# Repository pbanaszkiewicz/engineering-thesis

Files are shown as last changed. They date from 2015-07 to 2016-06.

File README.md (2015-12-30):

# Emergency Stop for an Autonomous Vehicle
## A Bachelor's Engineering Thesis project

This repository contains my BEng Thesis and project files.
The Thesis itself will be in Polish, but other resources should be
in English.

## Compilation

You can create a `main.pdf` containing the Thesis with following command:

```bash
$ make pdf
```

To remove all the debris from LaTeX use `make clean`.

## Credits

LaTeX class for AGH-UST specific representation of the Thesis was made by
M. Szpyrka and others (see `aghdpl.cls` for more).

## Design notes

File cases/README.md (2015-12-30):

Module cases
============

Cases presented here are based on the Arduino Leonardo and Uno containers done by
Zygmunt Wojcik (@zygmuntw).

Original work: https://github.com/zygmuntw/3D-Printed-Case-for-Arduino

# License

Zygmunt's work (and therefore this work) is licensed under
[Creative Commons Attribution-ShareAlike 3.0 Unported](http://creativecommons.org/licenses/by-sa/3.0/)
license.

# Modifications

Modifications I introduced:

* removed wholes for USB and other plugs
* moved PCB legs so that they work with Arduino Pro
* PCB legs: instead of pins I made wells (ie. substract instead of union)
* resized the case for module B and moved PCB legs around a little.

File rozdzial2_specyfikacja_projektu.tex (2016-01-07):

\chapter{Wykonanie projektu}
\label{cha:specyfikacja_projektu}

W tym rozdziale opisane zostało wykonanie projektu zgodnie z wymaganiami postawionymi w rozdziale \ref{cha:wstep}.

%---------------------------------------------------------------------------

\section{Opis części sprzętowej}
\label{sec:opis_cz_sprzetowej}

W poniższym rozdziale została opisana platforma sprzętowa modułów A i B oraz ich współdziałanie z innymi komponentami, m.in. z zasilaniem akumulatorowym czy z przekaźnikiem w samochodzie elektrycznym.

\subsection{Moduł A}
\label{subsec:modul_a}

Jest to moduł bazowy, tj. trzymany przez operatora w dłoni. Ze względu na użycie Arduino Pro 328 5V 16MHz \cite{Ard00} (zob. zdjęcie \ref{fig:arduino_pro}) jako platformy sprzętowej, ma on niewielkie wymiary.

\begin{figure}[h]
	\centering
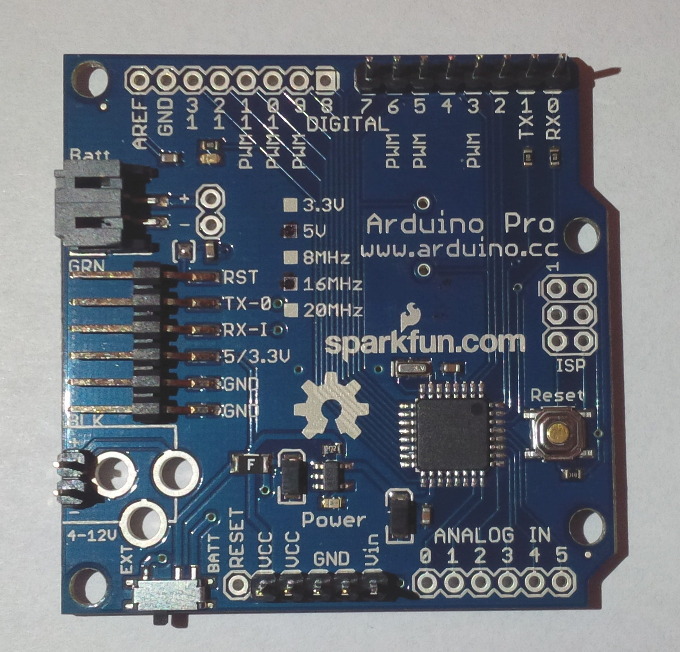
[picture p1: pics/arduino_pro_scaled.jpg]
	
	\caption{\label{fig:arduino_pro}Platforma sprzętowa Arduino Pro 328 5V 16MHz (zdjęcie: Piotr Banaszkiewicz).}
\end{figure}

\raggedbottom

\subsection{Moduł B}
\label{subsec:modul_b}

Jest to moduł, który został zamontowany w samochodzie. Jako platformę użyte zostało ponownie Arduino Pro 328 5V 16MHz \cite{Ard00} (zob. zdjęcie \ref{fig:arduino_pro}). Podstawowa funkcja, tj. odłączanie i załączanie silnika elektrycznego, odbywa się za pomocą przekaźnika ASR-90DD-H firmy Anly Electronics (zob. zdjęcie \ref{fig:SSR_relay} i rozdział \ref{subsec:odlaczanie_zalaczanie_silnika}).

\begin{figure}[h]
	\centering
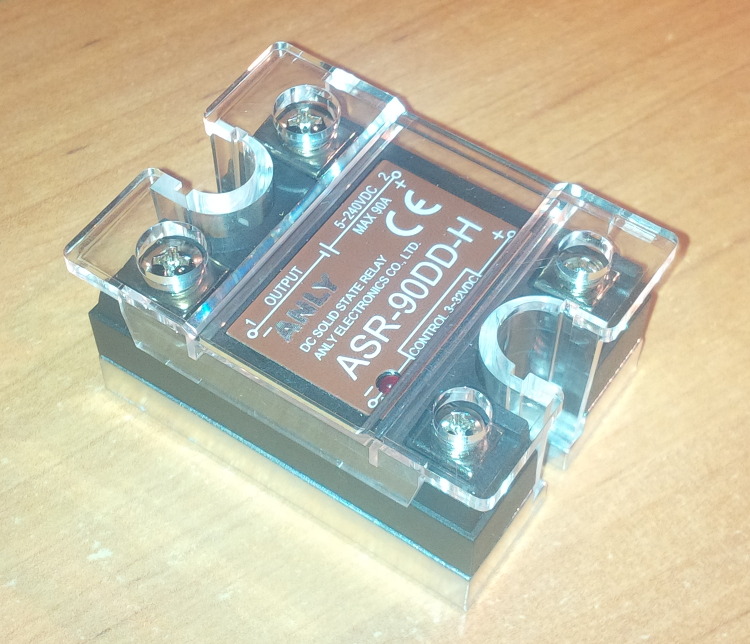
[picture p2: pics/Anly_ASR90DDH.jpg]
	
	\caption{\label{fig:SSR_relay}Przekaźnik półprzewodnikowy ASR-90DD-H  (zdjęcie: Piotr Banaszkiewicz).}
\end{figure}

\subsection{Zasilanie}
\label{subsec:zasilanie}

Obydwa moduły sprzętowe są zasilane z powerbanków Solo5 10000 mAh firmy Romoss. Posiadają one wbudowane różne zabezpieczenia, m.in.: natężeniowe (dla zachowania żywotności), temperaturowe czy zwarciowe (ang. \textit{short-circuit}). Mają również układ, który wyłącza powerbank w sytuacji, gdy prąd ładowania jest bardzo niewielki \cite{Romoss}.

Moduły A i B pobierają bardzo niewiele prądu (zmierzone: między \SI{20}{\milli\ampere} a \SI{50}{\milli\ampere}), więc aby powstrzymać powerbanki przed rozłączaniem zwarto masę i źródło energii dwunastoma (w przypadku modułu A) lub trzynastoma (w przypadku modułu B) rezystorami \SI{910}{\ohm} wpiętymi równolegle.

Połączenie równoległe takiej ilości rezystorów daje dość niską rezystancję zastępczą (teoretycznie: \SI{75.83}{\ohm} dla modułu A, \SI{70}{\ohm} dla modułu B; praktycznie: występują różnice w faktycznych wartościach rezystancji rezystorów, zwłaszcza gdy te się nagrzeją) i pozwala na obniżenie wydzielanego ciepła na rezystorach, co skutkuje:

\begin{itemize}
\item większym poborem prądu, dzięki czemu powerbanki się nie wyłączają,
\item nagrzewaniem rezystorów (z prawa Ohma: $ P = \dfrac{U^2}{R} = \dfrac{(5,1)^2}{900} = 0,0289 [W] $, gdzie \SI{5.1}{\volt} to zmierzone napięcie na rezystorze, a \SI{900}{\ohm} to przybliżona rezystancja nagrzanego rezystora), a więc w przypadku 12 rezystorów położonych bardzo blisko siebie mamy około \SI{0.34}{\watt} wydzielanej mocy w tym miejscu.
\end{itemize}

Ponadto banki energii umożliwiają jednoczesne ładowanie jak i rozładowywanie, tzn. jest możliwe wpięcie źródła zasilania na wejście powerbanku, jak i obciążenia na jego wyjście. Dzięki temu powerbank zasilający moduł B można ładować z portu USB znajdującego się w~samochodzie.

Sama pojemność \SI{10000}{\milli\ampere\hour} teoretycznie\footnote{W praktyce pojemność \SI{10000}{\milli\ampere\hour} jest nieosiągalna, gdyż powerbanki posiadają mechanizmy wydłużające ich żywotność; polega to na ładowaniu akumulatorów powerbanku tylko do pewnego stopnia.} pozwala na zasilanie układu pobierającego \SI{100}{\milli\ampere} przez 100 godzin lub układu pobierającego \SI{200}{\milli\ampere} przez 50 godzin. Każdy z modułów A i B po obciążeniu przez rezystory pobierał między \num{100} a \SI{200}{\milli\ampere}. Poziom naładowania powerbanków można obserwować na ich diodowych wskaźnikach.

\subsection{Komunikacja}
\label{subsec:komunikacja}

Do komunikacji wykorzystano parę modułów radiowych HC-12 433 MHz \cite{HC12}, które łączą się z~platformami sprzętowymi za pomocą łącza szeregowego. Prędkość komunikacji takiego modułu w powietrzu wynosi 5000bps, czyli typowe pakiety przesyłane przez system (zob. rozdział \ref{subsec:format_pakietow}), mające rozmiar $ 4B=32b $ są przesyłane w ułamku sekundy.

\subsection{Obudowy}
\label{subsec:obudowy}

Dla każdego modułu systemu ESAV przygotowano sztywną nakładkę w formie płytki prototypowej (zdjęcia \ref{fig:moduleA_hat} i \ref{fig:moduleB_hat}) z~przylutowanymi komponentami wykorzystywanymi przez dany moduł. Zakładane są one na górne i dolne piny modułów A i B (zob. zdjęcie \ref{fig:arduino_pro}).

\begin{figure}[h]
	\centering
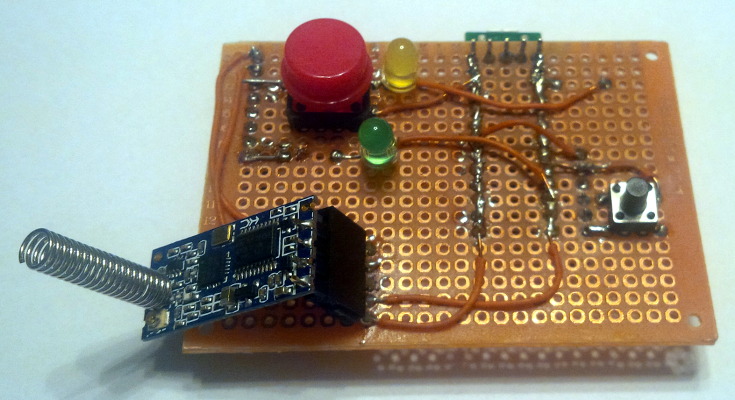
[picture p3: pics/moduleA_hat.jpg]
	
	\caption{\label{fig:moduleA_hat}Nakładka na moduł A (zdjęcie: Piotr Banaszkiewicz).}
\end{figure}

\begin{figure}[h]
	\centering
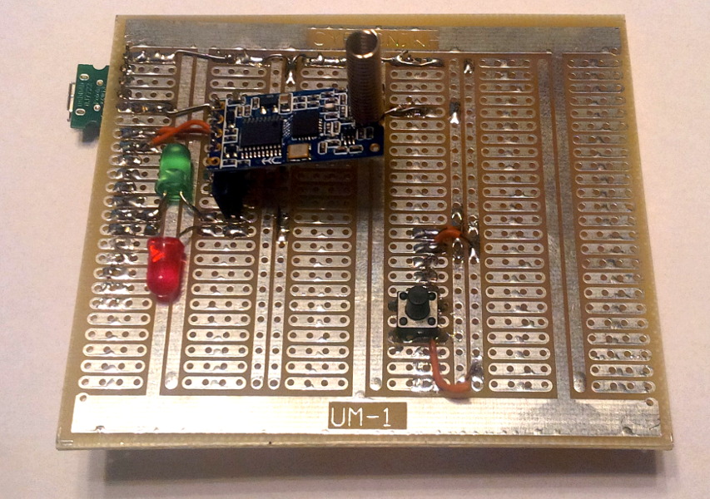
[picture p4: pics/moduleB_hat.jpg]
	
	\caption{\label{fig:moduleB_hat}Nakładka na moduł B (zdjęcie: Piotr Banaszkiewicz).}
\end{figure}

Ponadto na każdą platformę została zaprojektowana obudowa. Na zdjęciu \ref{fig:arduino_pro} widać cztery otwory w platformie Arduino (dwa przy lewej krawędzi płytki PCB oraz dwa przy prawej krawędzi), które zostały użyte do przykręcenia każdej z platform do obudowy.

Obudowy bazują na istniejącym projekcie kontenerów dla Arduino Leonardo oraz Uno wykonanym przez Zygmunta Wojcika  \cite{Woj15}. Ich licencja zezwala na modyfikacje (więcej szczegółów dostępnych jest pod adresem \cite{CasesLicense}).

\begin{figure}[H]
	\centering
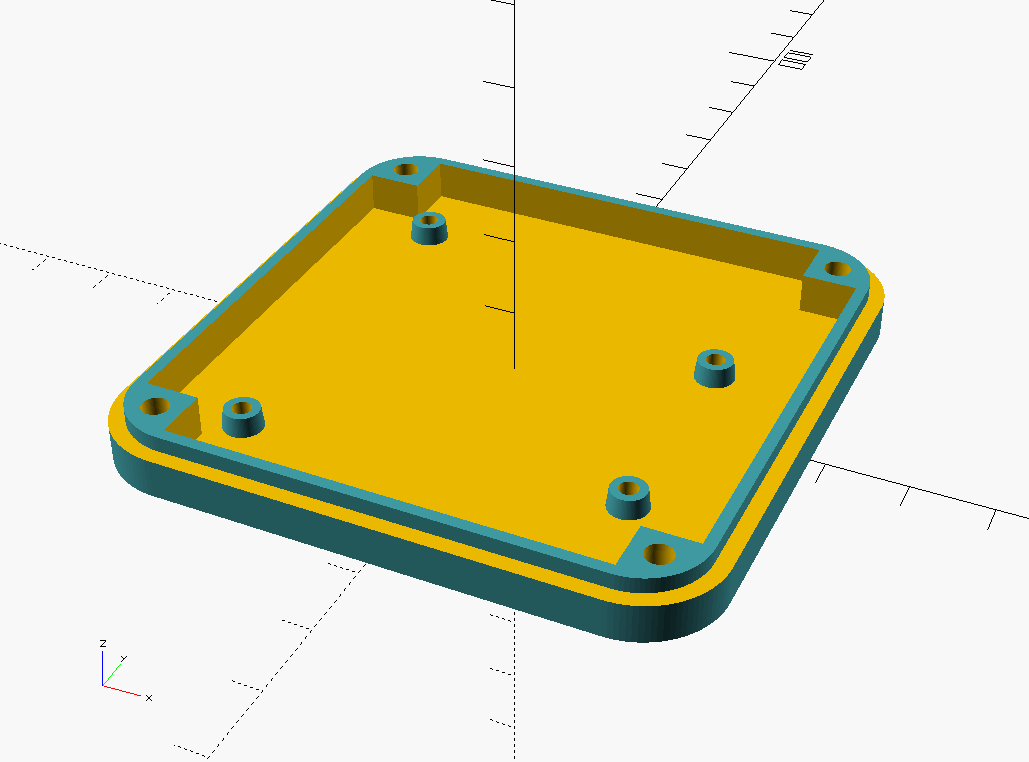
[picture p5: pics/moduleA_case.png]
	
	\caption{\label{fig:moduleA_case}Obudowa modułu A (oryginalny autor: Zygmunt Wojcik, modyfikacje: Piotr Banaszkiewicz \cite{CasesLicense}).}
\end{figure}

\begin{figure}[H]
	\centering
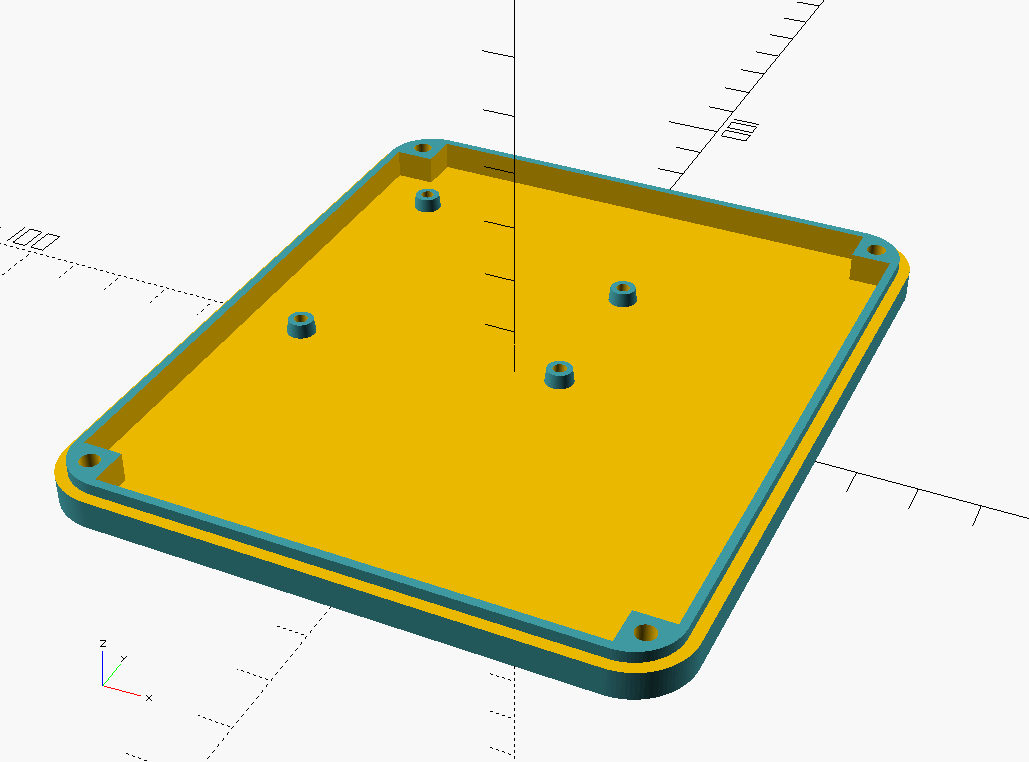
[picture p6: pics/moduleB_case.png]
	
	\caption{\label{fig:moduleB_case}Obudowa modułu B (oryginalny autor: Zygmunt Wojcik, modyfikacje: Piotr Banaszkiewicz \cite{CasesLicense}).}
\end{figure}

\subsection{Schematy połączeń}
\label{subsec:schematy_polaczen}

Symboliczny sposób połączenia modułu A, wejścia zasilającego USB oraz transceivera radiowego został przedstawiony na schemacie \ref{fig:symbolic_schema_A}.

\begin{figure}[H]
	\centering
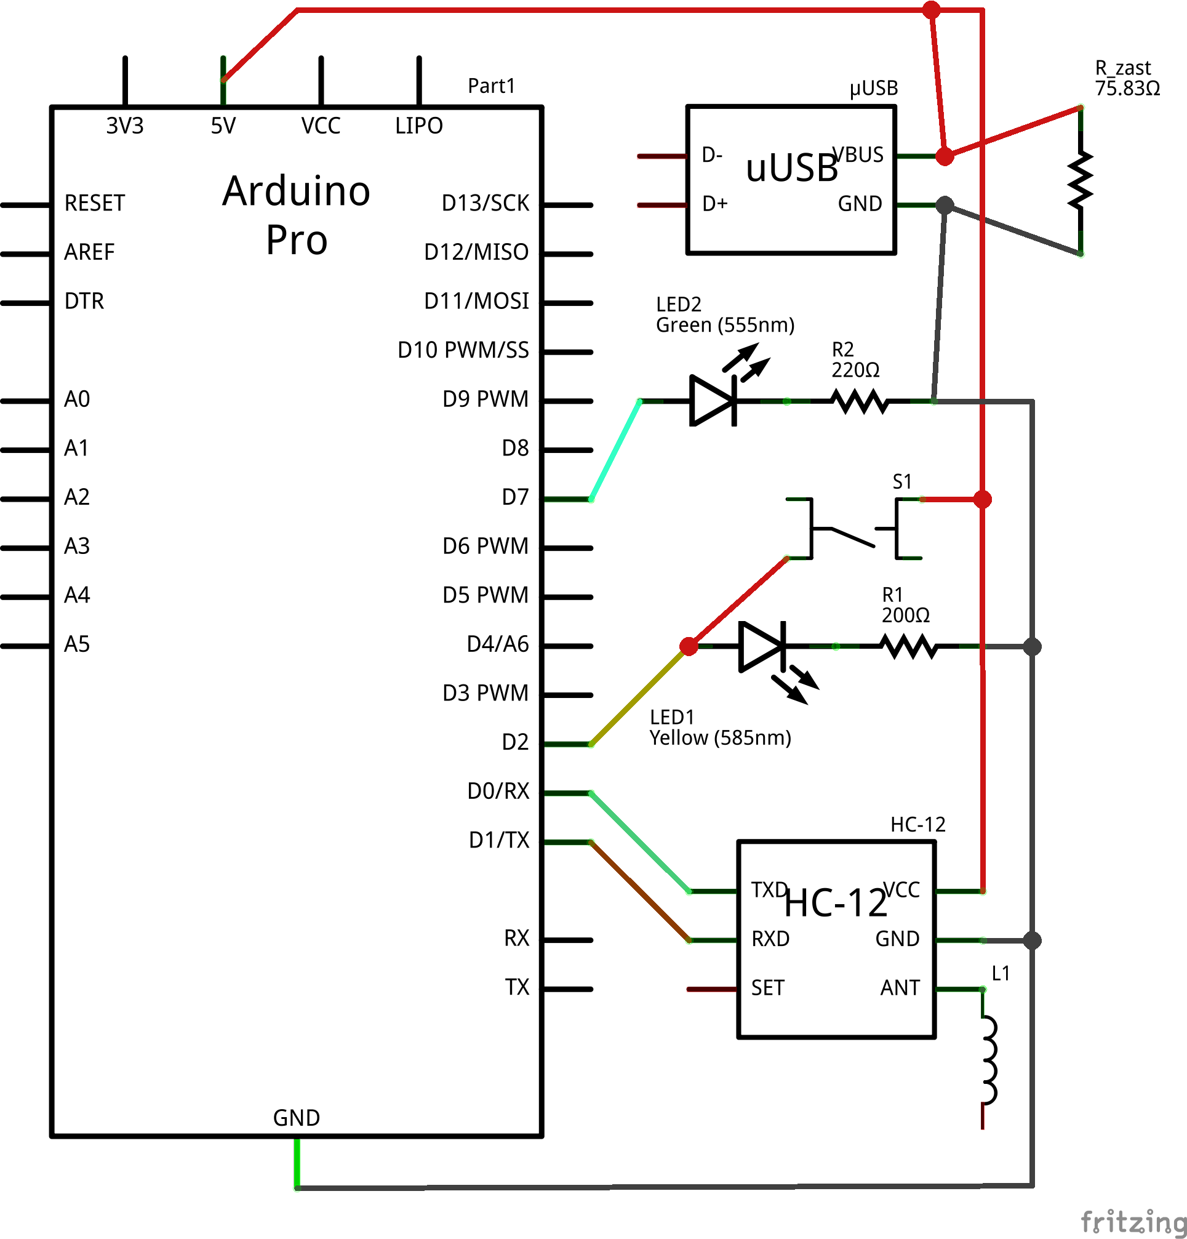
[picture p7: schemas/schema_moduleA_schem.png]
	
	\caption{\label{fig:symbolic_schema_A}Schemat połączeń modułu A wygenerowany w programie Fritzing \cite{Fritzing} (opracowanie własne).}
\end{figure}

Bardzo podobnie wygląda symboliczny schemat połączeń modułu B, z tym że on dodatkowo steruje przekaźnikiem (schemat \ref{fig:symbolic_schema_B}).

\begin{figure}[H]
	\centering
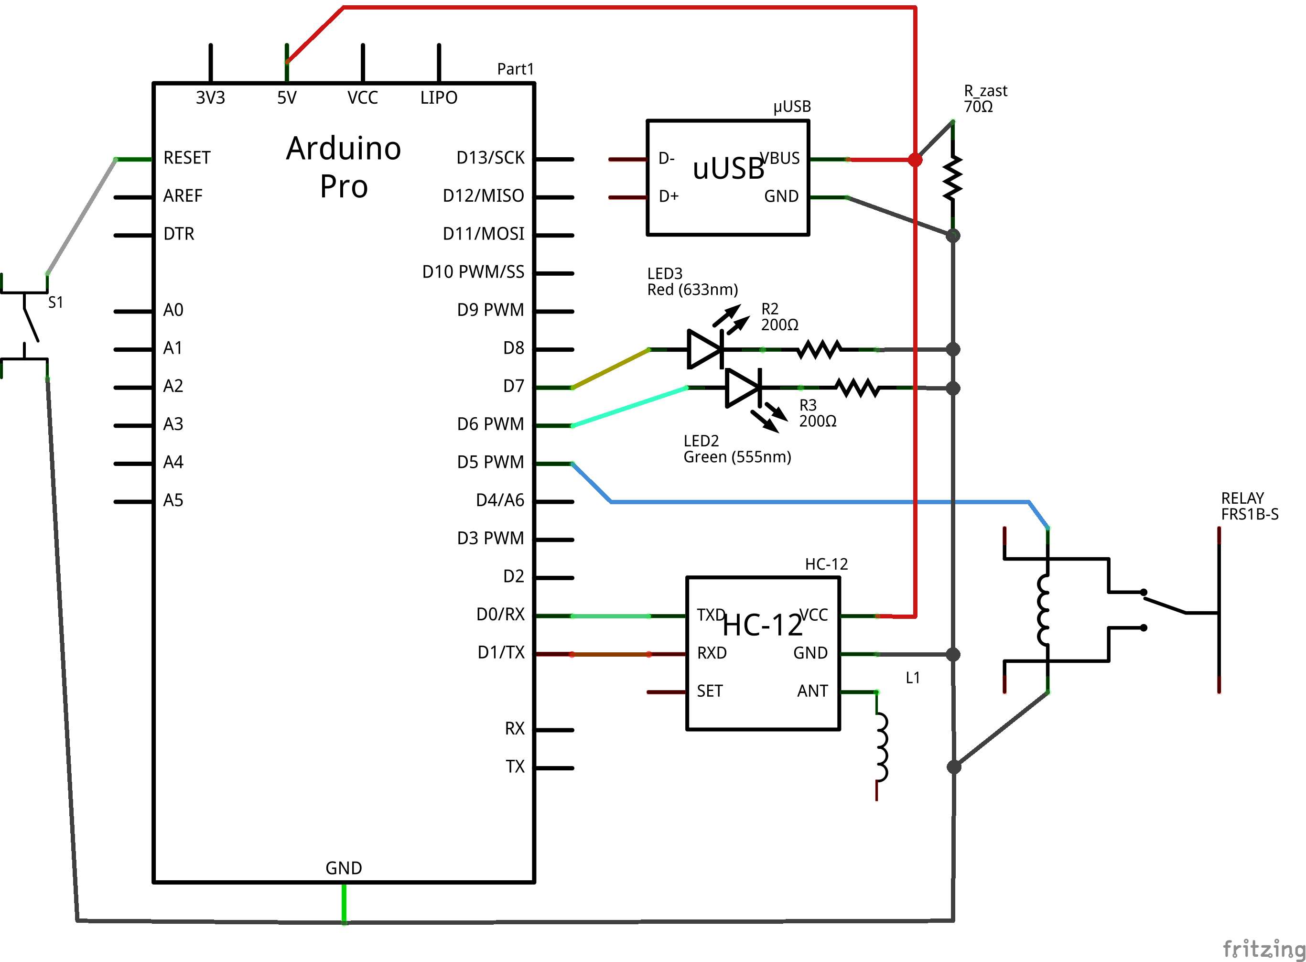
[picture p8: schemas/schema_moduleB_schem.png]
	
	\caption{\label{fig:symbolic_schema_B}Schemat połączeń modułu B wygenerowany w programie Fritzing \cite{Fritzing} (opracowanie własne).}
\end{figure}

\subsection{Odłączanie i załączanie silnika samochodu}
\label{subsec:odlaczanie_zalaczanie_silnika}

Pomiędzy kabel zasilający a moduł sterujący pracą silnika samochodu został wpięty przekaźnik ASR-90DD-H (zob. zdjęcie \ref{fig:SSR_relay}). Moduł sterujący odpowiedzialny jest za przetworzenie napięcia stałego na prąd zmienny poprowadzony bezpośrednio na uzwojenia silnika.

Przekaźnik ASR-90DD-H jest to przekaźnik półprzewodnikowy, a zatem typu \textit{Normally Open}, sterowany napięciem stałym \num{3}--\SI{32}{\volt}. Przekaźnik jest sterowany wyjściem z modułu B (zob. element ,,RELAY'' na schemacie \ref{fig:symbolic_schema_B}).

Według danych producenta, przekaźnik jest w stanie obsłużyć na wyjściu mocy do \SI{90}{\ampere} prądu stałego pod napięciem do \SI{240}{\volt}. Wybrano przekaźnik mocno przekraczający spodziewane natężenie prądu, gdyż zapewnia to mniejsze wydzielanie ciepła (zob. rozdział \ref{subsec:chlodzenie_SSR}).

Niestety producent nie udostępnia schematu elektrycznego przekaźnika w dokumentacji \cite{ASR90DDH}, więc podczas jego montażu zadbano o kilka elementów bezpieczeństwa:

\begin{itemize}
\item zastosowano podkładkę silikonową jako izolator elektryczny,
\item zastosowano radiator chłodzący (widoczny na zdjęciu \ref{fig:radiator}).
\end{itemize}

\begin{figure}[h]
	\centering
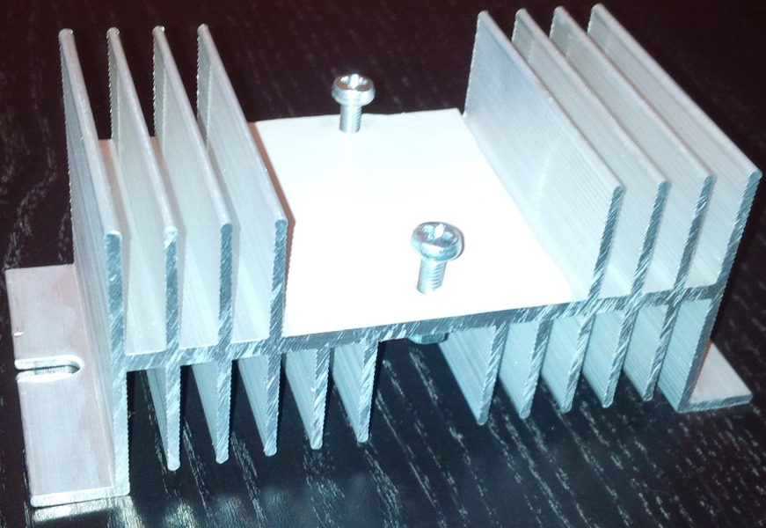
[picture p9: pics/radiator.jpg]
	
	\caption{\label{fig:radiator}Radiator chłodzący przekaźnik SSR (zdjęcie: Piotr Banaszkiewicz).}
\end{figure}

Elementy te zgodne są z zaleceniami polskiego producenta przekaźników, firmy Relpol \cite{RELPOL}.

\subsection{Chłodzenie przekaźnika półprzewodnikowego}
\label{subsec:chlodzenie_SSR}

Przekaźniki półprzewodnikowe z powodu pewnej niskiej oporności własnej w momencie podłączonego wyjścia mocy wydzielają dużą ilość energii w postaci ciepła.

W ramach pracy inżynierskiej przeprowadzono eksperyment polegający na zmierzeniu temperatury obudowy działającego przekaźnika podczas włączonego obciążenia.

Przekaźnik został umieszczony na radiatorze i pracował przez kilka minut (do momentu ustalenia się temperatury) pod stałym obciążeniem. Kamera termowizyjna ostawiona była tak, by mierzyć temperaturę radiatora oraz obudowy przekaźnika. Tabela \ref{tab:eksperyment} zawiera zestawienie długości czasu działania przekaźnika pod obciążeniem, a także uzyskanej na końcu eksperymentu temperatury, natomiast zdjęcia \ref{fig:flir1} i \ref{fig:flir2} ukazują obrazy z kamery termowizyjnej.

\begin{table}[h]
    \centering
    
    \begin{threeparttable}
        \caption{Parametry eksperymentu obciążenia przekaźnika półprzewodnikowego}
        \label{tab:eksperyment}
        
        \begin{tabularx}{0.9\textwidth}{ccccX}
            \toprule
            Czas obciążenia & Napięcie & Natężenie & Temperatura radiatora\tnote{a} & Temperatura obudowy przekaźnika\tnote{a} \\
            \midrule
            \SI{8}{\minute} & \SI{45}{\volt} & \SI{36}{\ampere} & \SI{25}{\celsius} & ok. \SI{60}{\celsius} \\
            \SI{8}{\minute} & \SI{42.5}{\volt} & \SI{43}{\ampere} & \num{25}--\SI{35}{\celsius} & ok. \SI{90}{\celsius} \\
            \bottomrule
        \end{tabularx}
        
        \begin{tablenotes}
            \footnotesize
            \item[a] pod koniec pomiaru
        \end{tablenotes}
        
    \end{threeparttable}
\end{table}

\begin{figure}[H]
	\centering
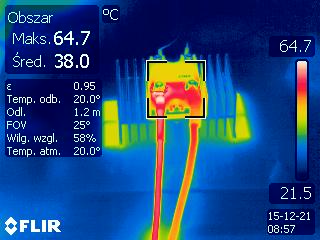
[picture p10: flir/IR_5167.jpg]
	
	\caption{\label{fig:flir1}Obraz uzyskany za pomocą kamery termowizyjnej na koniec trwania eksperymentu z mniejszym obciążeniem (zdjęcie: Marek Długosz).}
\end{figure}

\raggedbottom

\begin{figure}[H]
	\centering
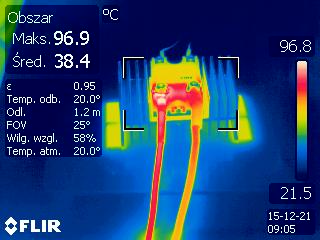
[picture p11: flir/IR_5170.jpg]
	
	\caption{\label{fig:flir2}Obraz uzyskany za pomocą kamery termowizyjnej na koniec trwania eksperymentu z większym obciążeniem (zdjęcie: Marek Długosz).}
\end{figure}

Na powyższych zdjęciach najcieplejszym elementem była śruba służąca do przykręcenia kabla zasilającego. Temperatura ciepłego miejsca na obudowie przekaźnika była o około \SI{15}{\celsius} niższa; uwzględnione to zostało w tabeli \ref{tab:eksperyment} poprzez odjęcie ok. \SI{10}{\celsius} od maksymalnej mierzonej temperatury.

Ponadto należy zauważyć jak niewiele nagrzewał się radiator, do którego przymocowany został przekaźnik. To udowadnia, że jest on wystarczający dla zastosowania w samochodzie.

Na samym końcu należy zauważyć, że przekaźnik nie powinien być w realnych zastosowaniach narażony na tak duże obciążenia przez tak długi czas; według obserwacji, maksymalny prąd chwilowy w trakcie przyspieszania pojazdu i skręcania jednocześnie wynosił około \SI{50}{\ampere}.

%---------------------------------------------------------------------------

\section{Opis części programowej}
\label{sec:opis_cz_programowej}

W tym rozdziale opisano m.in. logikę, algorytmy i struktury danych wykorzystywane przez programy modułów A i B.

\subsection{Schematy cykli-działań}
\label{subsec:schematy_cykli_dzialan}

Poniższe schematy reprezentują logikę, zdarzenia oraz czynności, jakimi posługują się moduły A~i~B.

Dokładny opis pakietów danych oraz momenty, w których są przesyłane, znajduje się w rozdziale \ref{subsec:format_pakietow}.

\raggedbottom

\begin{figure}[H]
	\centering
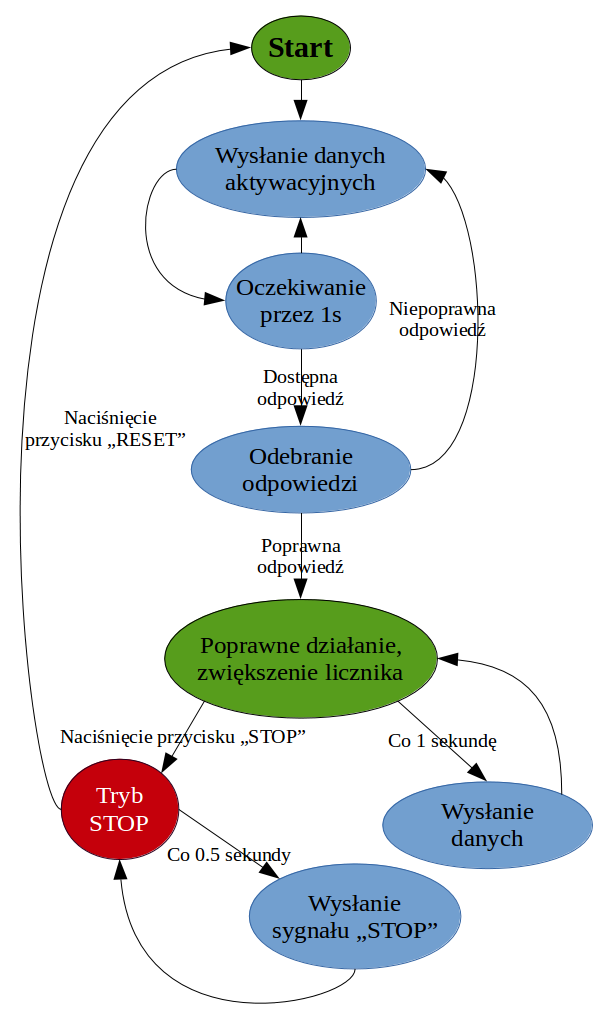
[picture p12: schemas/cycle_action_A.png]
	
	\caption{\label{fig:cycle_action_A}Graf cykli-działań dla modułu A (opracowanie własne).}
\end{figure}

\begin{figure}[H]
	\centering
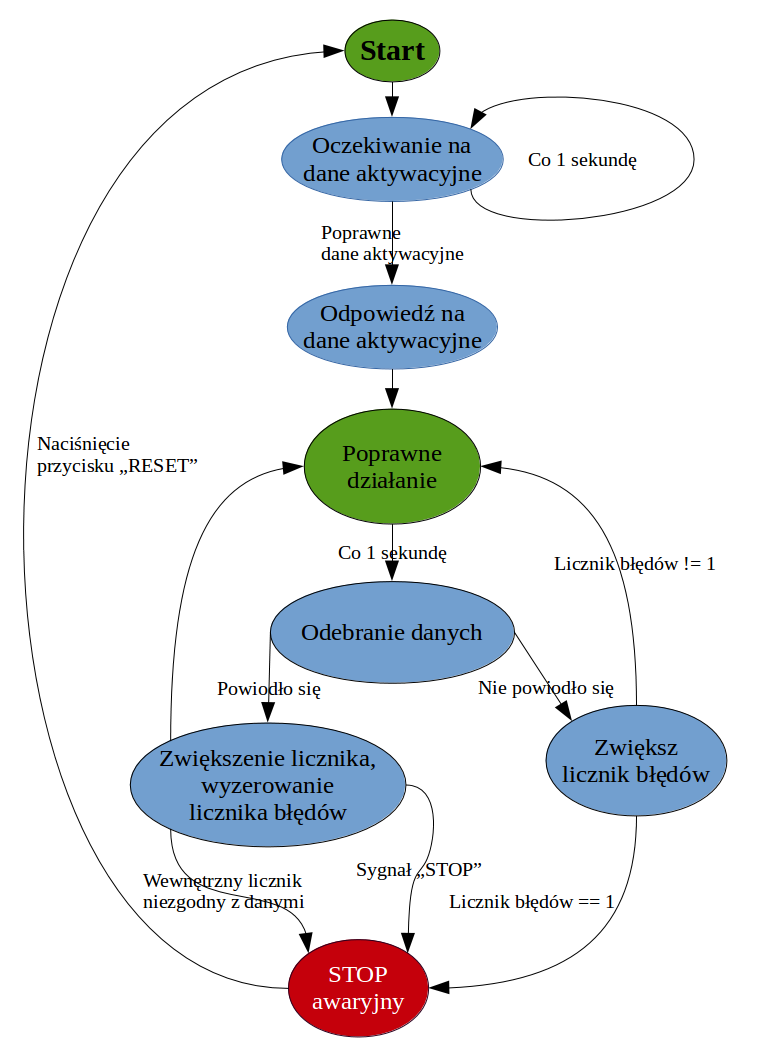
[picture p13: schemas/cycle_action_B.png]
	
	\caption{\label{fig:cycle_action_B}Graf cykli-działań dla modułu B (opracowanie własne).}
\end{figure}

\subsection{Format pakietów}
\label{subsec:format_pakietow}

Każdy pakiet ma długość 4 bajtów:

\begin{equation}
0 \mathrm{x} \underbrace{\mathrm{FC}}_\text{e}  \underbrace{\mathrm{ABCD}}_\text{c} \underbrace{00}_\text{s}
\end{equation}
gdzie
\begin{eqwhere}[2cm]
	\item[$e$] bajt \textit{emergency}. Jeżeli jego wartość to $0xFF$ to moduł B ma natychmiast przejść do trybu awaryjnego. W praktyce oznacza to, że operator wcisnął przycisk ,,STOP'' modułu A.
	\item[$c$] 2 bajty zapisujące wartość liczbową licznika modułu A (typ bez znaku, 16 bitów),
	\item[$s$] bajt stopu, jego wartość zawsze ma być równa $0x00$.
\end{eqwhere}

Istnieją 2 pakiety specjalne przesyłane między modułami A i B w celu synchronizacji i rozpoczęcia działania:

\begin{itemize}
\item pakiet danych aktywacyjnych wysyłany przez moduł A: $0\mathrm{xFFFFFF}00$,
\item pakiet odpowiedzi na dane aktywacyjne wysyłany przez moduł B: $0\mathrm{x11FFFF}00$,
\item ponadto każdy pakiet danych wysyłany przez moduł A już po odebraniu odpowiedzi na dane aktywacyjne zawiera bajt \textit{emergency} ustawiony na wartość $0\mathrm{x}22$ -- za wyjątkiem sytuacji, w której moduł A żąda od modułu B przejścia w tryb awaryjny; wtedy ten bajt ustawiony jest na wartość $0\mathrm{xFF}$.
\end{itemize}

Przykładowe pakiety:

\begin{itemize}
\item $0\mathrm{x}223\mathrm{F}0\mathrm{E}00$: moduł A wysyła informację o braku konieczności przejścia w tryb awaryjny oraz o wartości licznika (16142),
\item $0\mathrm{xFFA}37800$: moduł A wysyła informację o przejściu w tryb awaryjny oraz o ostatniej wartości licznika (41848).
\end{itemize}

\subsection{Maszyna stanów}
\label{subsec:maszyna_stanow}

Oprogramowanie modułów A i B wykorzystuje proste maszyny stanów \cite{Bro69}.

Stany modułu A:

\begin{enumerate}
\item CONNECTING: wysyłanie pakietu danych aktywacyjnych co 1 sekundę, oczekiwanie na odpowiedź,
\item PING: wysyłanie obecnej wartości licznika co 1 sekundę, zwiększanie wartości licznika,
\item STOP: wysyłanie ostatniej wartości licznika oraz ustawionego bajtu \textit{emergency} co $0.5$ sekundy.
\end{enumerate}

Stany modułu B:

\begin{enumerate}
\item WAIT: oczekiwanie na przyjście pakietu danych aktywacyjnych; odesłanie na niego odpowiedzi,
\item RUN: zwiększanie wewnętrznego licznika, odbieranie wartości licznika modułu A, porównywanie obu liczników, sprawdzanie bajtu \textit{emergency},
\item STOP: podtrzymywanie wyłączenia zasilania.
\end{enumerate}

Warunki przejścia między stanami modułu A:

\begin{itemize}
\item CONNECTING $\rightarrow$ PING: gdy pakiet odpowiedzi na dane aktywacyjne wysłany przez moduł B to $0\mathrm{x}11\mathrm{FFFF}00$,
\item PING $\rightarrow$ STOP: gdy operator wciśnie przycisk ,,RESET''.
\end{itemize}

Warunki przejścia między stanami modułu B:

\begin{itemize}
\item WAIT $\rightarrow$ RUN: gdy pakiet danych aktywujących wysłany przez moduł A to $0\mathrm{xFFFFFF}00$,
\item RUN $\rightarrow$ STOP: gdy jeden z warunków jest spełniony:
    \begin{itemize}
    \item bajt \textit{emergency} w przychodzącym pakiecie ma wartość $0\mathrm{xFF}$,
    \item licznik wewnętrzny ma wartość różną od wartości licznika wysłanej przez moduł A w przychodzącym pakiecie,
    \item przez 3 sekundy nie nadeszły żadne dane od modułu A.
    \end{itemize}
\end{itemize}

\subsection{Panel operatorski}
\label{subsec:panel_operatorski}

Obydwa moduły systemu ESAV zawierają minimalny interfejs dla użytkownika. Składa się on odpowiednio z:

\begin{itemize}
\item dla modułu A:
    \begin{itemize}
    \item przycisk ,,STOP'' wywołujący przerwanie wewnętrzne platformy Arduino i w konsekwencji wysłanie polecenia przejścia do trybu awaryjnego,
    \item przycisk ,,RESET'' do łatwiejszego restartu urządzenia,
    \item zieloną diodę informującą o wysyłaniu danych przez port szeregowy,
    \item żółtą diodę włączającą się w momencie naciśnięcia przycisku ,,STOP'' (spełnia ona funkcję wizualnego sprzężenia zwrotnego dla użytkownika),
    \end{itemize}
    
\item dla modułu B:
    \begin{itemize}
    \item przycisk ,,RESET'' do łatwiejszego restartu urządzenia,
    \item zieloną diodę informującą o poprawnym trybie pracy (stan ,,RUN''),
    \item czerwoną diodę informującą o oczekiwaniu na dane wejściowe (szybka pulsacja) lub o przejściu w tryb awaryjny (ciągłe świecenie).
    \end{itemize}
\end{itemize}

\subsection{Szyfrowanie komunikacji}
\label{subsec:szyfrowanie_komunikacji}

Komunikacja pomiędzy modułami (za wyjątkiem przekazywanych danych aktywacyjnych i odpowiedzi na nie) jest w prosty sposób szyfrowana.

Do szyfrowania wykorzystywane są dwie tablice, każda o długości 256, co odpowiada ilości wartości pojedynczego bajtu. Szyfrowanie pojedynczego bajtu polega na odszukaniu w tablicy szyfrującej odpowiadającej mu wartości zaszyfrowanej, a odszyfrowanie polega na odszukaniu w tablicy deszyfrującej wartości oryginalnej odpowiadającej wartości zaszyfrowanej.

Poniższy przykład ilustruje szyfrowanie i deszyfrowanie na przykładzie czterech wartości:

\begin{lstlisting}[frame=single,caption=Pseudokod zbliżony do C pokazujący zasadę szyfrowania i deszyfrowania komunikacji systemu ESAV.]
byte cipher_array[] = {3, 1, 0, 2};
byte decipher_array[] = {2, 1, 3, 0};
byte original = 2;
byte encrypted = cipher_array[original];
assert(original == decipher_array[encrypted]);
\end{lstlisting}

Dzięki wykorzystaniu tej prostej metody nie nastąpił żaden narzut w wielkości przesyłanych pakietów, niestety skutkiem słabszego bezpieczeństwa niż w przypadku stosowania np. algorytmu AES \cite{AESComment}.

\subsection{Programowanie Arduino}
\label{subsec:programowanie_arduino}

Platforma Arduino, na której oparty jest system ESAV, programowana jest w środowisku Arduino IDE (zob. \ref{fig:arduino_ide}) za pomocą języka bardzo zbliżonego do C. Opis jego składni, udostępnionych funkcji i klas dostępny jest w \cite{ArduinoRef}.

Podczas pracy nad projektem stworzono dwa pliki źródłowe, odpowiednio dla modułu A oraz B, a także jedną bibliotekę w C++ współdzieloną przez oba projekty, której zadaniem jest obsługiwanie szyfrowania i deszyfrowania komunikacji pomiędzy modułami.

Pliki źródłowe dostępne są w serwisie GitHub \cite{CodeSource}.

\begin{figure}[H]
	\centering
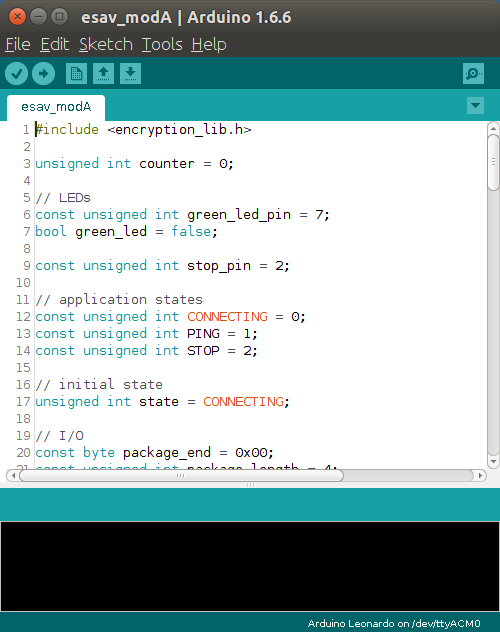
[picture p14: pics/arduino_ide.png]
	
	\caption{\label{fig:arduino_ide}Interfejs programu Arduino IDE używany do programowania na platformę Arduino (zdjęcie: Piotr Banaszkiewicz).}
\end{figure}

\subsection{Kabel do programowania Arduino}
\label{subsec:kabel_do_programowania_arduino}

Platforma Arduino Pro, w przeciwieństwie do innych większych mikrokontrolerów Arduino, nie zawiera programatora na USB. Programowanie Arduino Pro odbywa się poprzez port szeregowy (6 pinów usytuowanych równolegle do płytki PCB, widocznych po lewej stronie na zdjęciu \ref{fig:arduino_pro}).

\begin{figure}[h]
	\centering
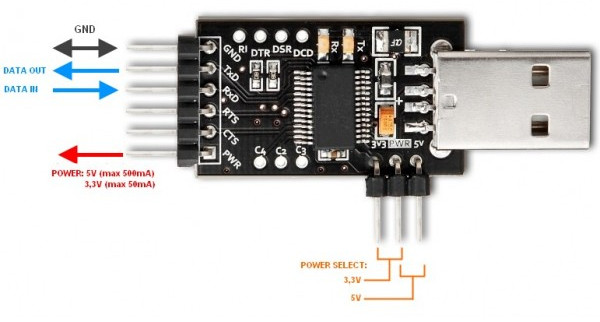
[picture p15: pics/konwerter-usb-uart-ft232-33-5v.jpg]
	
	\caption{\label{fig:konwerter}Opis wyjść używanego konwertera USB-UART (zdjęcie: Botland \cite{KonwerterBotland}).}
\end{figure}

Niestety używany konwerter USB-UART posiada zgodne wyprowadzenia (zob. \ref{fig:konwerter}), ale w nieodpowiedniej kolejności, co zostało przedstawione w tabeli \ref{tab:piny}.

\begin{table}[h]
    \centering
    
    \begin{threeparttable}
        \caption{Złącza komunikacji szeregowej i zasilania platformy Arduino Pro oraz używanego konwertera USB-UART.}
        \label{tab:piny}
        
        \begin{tabular}{cc}
            \toprule
            Wyprowadzenie Arduino Pro & Wyprowadzenie konwertera USB-UART \\
            \midrule
            RST & GND \\
            TX & TXD \\
            RX & RXD \\
            5V & RTS \\
            GND & CTS \\
            GND & PWR \\
            \bottomrule
        \end{tabular}
        
    \end{threeparttable}
\end{table}

Podłączenia wymagane do prawidłowego zaprogramowania Arduino Pro:

\begin{itemize}
\item RST $\rightarrow$ RTS
\item TX $\rightarrow$ RXD
\item RX $\rightarrow$ TXD
\item 5V $\rightarrow$ PWR
\item GND $\rightarrow$ GND
\end{itemize}

W związku z tym konieczne stało się stworzenie kabla pozwalającego łatwo programować moduły systemu ESAV. Został on zbudowany na podstawie tzw. skrętki ethernetowej (zdjęcie \ref{fig:cable}).

\begin{figure}[h]
	\centering
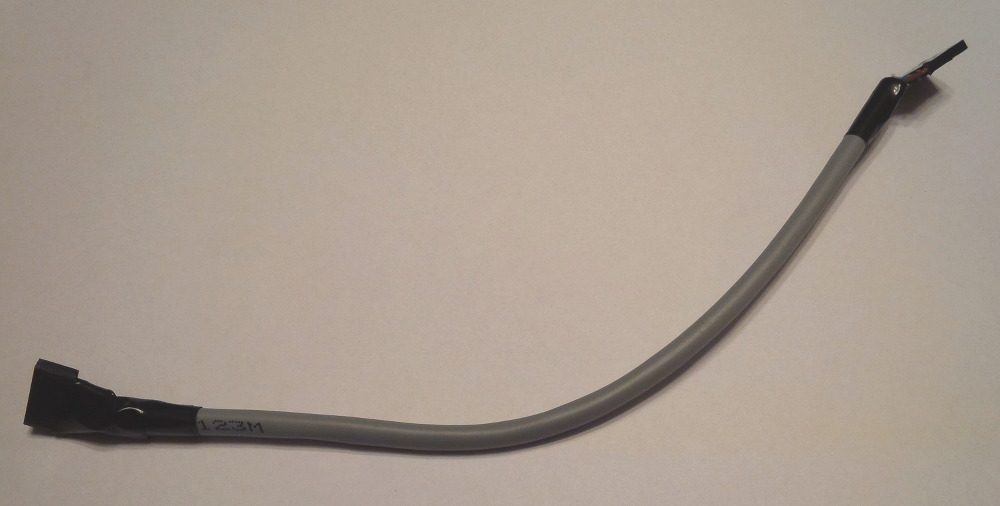
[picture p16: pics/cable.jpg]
	
	\caption{\label{fig:cable}Zdjęcie kabla wykorzystywanego do programowania Arduino (zdjęcie: Piotr Banaszkiewicz).}
\end{figure}

%---------------------------------------------------------------------------

\section{Zakres zrealizowanych wymagań}
\label{sec:zrealizowane_wymagania}

W poniższej tabeli zestawiono założenia projektu wyszczególnione w rozdziale wraz z informacją o ich spełnieniu (bądź wytłumaczeniem dlaczego nie zostały spełnione) oraz odnośnikiem do rozdziału zawierającego bardziej szczegółowe informacje na temat danej funkcjonalności.

\begin{longtable}{p{.15\textwidth} p{.15\textwidth} p{.15\textwidth} p{.35\textwidth} p{.05\textwidth}}
\caption{Macierz śledzenia wymagań (ang. \textit{requirements traceability matrix} \cite{Hug10}).} \label{tab:spelnione_wymagania} \\

\toprule
Numer wymagania & Wymagane? & Spełnione? & Jak? & Roz. \\
\midrule

\ref{wym_fun1} & Tak & Tak & Przekaźnik typu \textit{Normally Open}. & \ref{subsec:odlaczanie_zalaczanie_silnika} \\ \hline
\ref{wym_fun2} & Tak & Tak & Oprogramowanie modułów A~i~B. & \ref{subsec:schematy_cykli_dzialan} \\ \hline
\ref{wym_fun3} & Tak & Tak & Przekaźnik typu \textit{Normally Open} oraz oprogramowanie modułu B. & \ref{subsec:maszyna_stanow} \\ \hline
\ref{wym_fun4} & Tak & Tak & Oprogramowanie modułu B. & \ref{subsec:maszyna_stanow} \\ \hline
\ref{wym_fun5} & Tak & Tak & Oprogramowanie modułu B. & \ref{subsec:maszyna_stanow} \\ \hline
\ref{wym_fun6} & Tak & Tak & Oprogramowanie modułów A i B. & \ref{subsec:maszyna_stanow} \\ \hline
\ref{wym_fun7} & Tak & Tak & Podpięcie przycisku ,,RESET'' do pinu RESET modułu B. & \ref{subsec:panel_operatorski} \\ \hline
\ref{wym_fun8} & Tak & Tak & Przekaźnik typu \textit{Normally Open}. & \ref{subsec:odlaczanie_zalaczanie_silnika} \\ \hline
\ref{wym_fun9} & Nie & Nie & Zakupione powerbanki umożliwiają ładowanie podczas używania ich, jednakże to w gestii użytkownika jest korzystanie z tej możliwości. & \ref{subsec:zasilanie} \\ \hline
\ref{wym_uzyt1} & Tak & Tak & Powerbanki powinny teoretycznie zapewnić zasilanie przez około \num{50}--\num{100} godzin. & \ref{subsec:zasilanie} \\ \hline
\ref{wym_uzyt2} & Tak & Tak & Prędkość przesyłania danych między modułami HC-12 wynosi 5000bps. & \ref{subsec:komunikacja} \\ \hline
\ref{wym_uzyt3} & Tak & Tak & Przetestowano &  \\ \hline  %% podaj wartosc
\ref{wym_uzyt4} & Tak & Tak & Przetestowano &  \\ \hline  %% podaj wartosc
\ref{wym_wsp1} & Tak & Tak & Moduł B odłącza zasilanie modułu, który bezpośrednio zasila silnik samochodu. & \ref{subsec:odlaczanie_zalaczanie_silnika} \\ \hline
\ref{wym_wsp2} & Nie & Nie & Zakupione powerbanki umożliwiają ładowanie podczas używania ich, jednakże to w gestii użytkownika jest korzystanie z tej możliwości. & \ref{subsec:zasilanie} \\ \hline
\ref{wym_bezp1} & Tak & Tak & Wejście sterowania przekaźnika jest optoizolowane. & \ref{subsec:odlaczanie_zalaczanie_silnika} \\ \hline  %% aktualizuj bazujac na dokumentacji od ANLY?
\ref{wym_bezp2} & Tak & Tak & Komunikacja pomiędzy modułami polega na wymianie szyfrowanego licznika. & \ref{subsec:szyfrowanie_komunikacji} \\ \hline
\ref{wym_bezp3} & Tak & Tak & Przekaźnik dopiero wystawiony na bardzo długie działanie pod wysokim obciążeniem może osiągnąć temperaturę \SI{100}{\celsius}. & \ref{subsec:chlodzenie_SSR} \\ \hline
\ref{wym_poch1} & Nie & Nie & Poziom naładowania jest wyświetlany na obudowie powerbanku, więc nie ma konieczności dodatkowego monitorowania przez moduł B. & \ref{subsec:zasilanie} \\ \hline
\ref{wym_poch2} & Tak & Tak & Spełnione dosłownie. & \ref{subsec:panel_operatorski} \\ \hline
\ref{wym_poch3} & Tak & Tak & Spełnione dosłownie. & \ref{subsec:panel_operatorski} \\ \hline
\ref{wym_poch4} & Tak & Tak & Spełnione dosłownie. & \ref{subsec:panel_operatorski} \\ \hline
\ref{wym_poch5} & Nie & Nie & Poziom naładowania jest wyświetlany na obudowie powerbanku, więc nie ma konieczności dodatkowego monitorowania przez moduł B. & \ref{subsec:zasilanie} \\ \hline
\ref{wym_poch6} & Tak & Tak & Spełnione dosłownie. & \ref{subsec:panel_operatorski} \\ \hline
\ref{wym_poch7} & Tak & Tak & Spełnione dosłownie. & \ref{subsec:obudowy} \\ \hline
\ref{wym_poch8} & Tak & Tak & Wysłanie pakietu danych jest rozumiane jako ,,PING''. & \ref{subsec:format_pakietow} \\ \hline
\ref{wym_poch9} & Tak & Tak & Opisane w formacie pakietów. & \ref{subsec:format_pakietow} \\ \hline
\ref{wym_poch10} & Nie & Nie & Niewymagane. &  \\ \hline

\bottomrule
\end{longtable}

%---------------------------------------------------------------------------

\section{Podsumowanie}
\label{sec:podsumowanie_specyfikacja_projektu}

Wykonanie projektu zostało podzielone na dwie części: część związaną stricte ze sprzętem oraz część związaną z programowaniem. Każda część wiązała się z innymi trudnościami, ale koniec końców wszystkie zostały pokonane.

Dzięki opisaniu wszystkich wymagań w rozdziale \ref{cha:wstep}, możliwe zostało ułożenie tabeli \ref{tab:spelnione_wymagania}, która od razu pokazuje w jakim stanie ukończenia jest projekt.

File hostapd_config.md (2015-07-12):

# WLAN Access Point on Raspberry Pi

Install `hostapd` software: `sudo aptitude install hostapd`.

Configure `hostapd` (`/etc/hostapd/hostapd.conf` may not exists, create if needed):

```
interface=wlan0
driver=nl80211
ssid=My_AP
hw_mode=g
channel=6
macaddr_acl=0
auth_algs=1
ignore_broadcast_ssid=0
wpa=2
wpa_passphrase=My_Passphrase
wpa_key_mgmt=WPA-PSK
wpa_pairwise=TKIP
rsn_pairwise=CCMP
```

Configure `hostapd` to load that config on start (`/etc/default/hostapd`), add line:

```
DAEMON_CONF="/etc/hostapd/hostapd.conf"
```

Then, to run `hostapd`: `sudo service hostapd start`.

To get `hostapd` running upon boot: `sudo update-rc.d hostapd enable`.

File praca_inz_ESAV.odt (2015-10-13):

Specyfikacja wymagań projektu Emergency Stop for an Autonomous Vehicle (ESAV)

# Statement of need – deklaracja potrzeb

Laboratorium pojazdów autonomicznych AGH—Delphi ma za zadanie zbudowanie pojazdu autonomicznego na bazie udostępnionego pojazdu elektrycznego. Podczas prac konieczne jest zapewnienie bezpieczeństwa podczas testowania algorytmów sterowania. Algorytmy takie mogą nie działać poprawnie, w związku z czym w trakcie testów może zajść potrzeba awaryjnego przerwania jazdy samochodu.

# Statement of work – cele projektu

System ESAV powinien charakteryzować się następującymi właściwościami:

1. Możliwość natychmiastowego zatrzymania pojazdu na polecenie operatora.
2. Możliwość natychmiastowego zatrzymania pojazdu w przypadku utraty zasilania systemu ESAV.
3. Możliwość natychmiastowego zatrzymania pojazdu w przypadku przerwania transmisji pomiędzy modułami systemu ESAV.
4. Możliwość natychmiastowego zatrzymania pojazdu w przypadku zakłóceń pracy systemu ESAV (np. błędy transmisji).
5. Możliwość poruszania się pojazdu tylko jeśli system ESAV jest zasilany.
6. Możliwość poruszania się pojazdu tylko w przypadku rozpoczęcia prawidłowej transmisji danych.
7. Możliwość wyświetlania aktualnego stanu systemu ESAV.

System ESAV składa się z dwóch części: modułu bazowego (moduł A) i modułu montowanego w pojeździe (moduł B).

System ESAV powinien posiadać swoje własne zasilanie całkowicie niezależne od zasilania pojazdu. sygnalizacja przy pomocy prostego systemu diod LED i sygnałów dźwiękowych.

Po wyłączeniu pojazdu przez system ESAV, na skutek błędów transmisji albo awaryjnego stopu, układ musi zostać ręcznie zresetowany, tzn. przywrócony do pracy.

Włączanie i wyłączanie systemu ESAV (modułu montowanego w pojeździe) zabezpieczone jest przez przełącznik z kluczykiem.

System ESAV musi umożliwiać łatwą wymianę baterii, monitorować i pokazywać poziom jej naładowania.

Po zdefiniowanym okresie bezczynności system ESAV powinien się sam wyłączyć.

System ESAV powinien być systemem bezobsługowym: raz skonfigurowany powinien poprawnie pracować.

## Functional requirements

1. Po włączeniu systemu powinien się on uruchomić i oczekiwać na dane aktywujące jego pracę. Stan systemu sygnalizowany jest migającą czerwoną diodą.
2. Dopóki system ESAV nie odbierze danych aktywujących, pojazd nie może się poruszać.
3. Po odebraniu danych aktywujących, system ESAV powinien umożliwić jazdę samochodu. Stan systemu sygnalizowany jest ciągle włączoną zieloną diodą LED.
4. Jeżeli podczas działania system ESAV po określonym czasie przestanie odbierać transmisję, system przejdzie w tryb awaryjny. Stan systemu sygnalizowany jest ciągle świecącą się czerwoną diodą LED.
5. Po naciśnięciu przycisku wyłączania awaryjnego na module A przez operatora, system ESAV przechodzi w tryb awaryjny. Stan systemu sygnalizowany jest ciągle świecącą się czerwoną diodą LED.
6. Po zresetowaniu modułu B poprzez naciśnięcie przycisku „Reset”, system ESAV powraca z trybu awaryjnego do stanu oczekiwania na dane aktywujące.
7. Po wyłączeniu zasilania modułu B, system ESAV przechodzi w tryb awaryjny.
8. Bateria systemu ESAV jest ładowana w trakcie ładowania akumulatorów pojazdu.

## Performance requirements

1. System ESAV powinien pracować bez konieczności wymiany bądź ładowania baterii przez minimum 5 godzin.
2. System ESAV powinien być w stanie co 1 sekundę odebrać i zdekodować dane.
3. System ESAV powinien prawidłowo pracować na dystansie 30 metrów.
4. System ESAV powinien prawidłowo pracować w pomieszczeniach.

## Integration requirements

1. Moduł B systemu ESAV musi działać poprawnie z szeregowo podłączonymi akumulatorami w pojeździe.
2. Moduł B musi mieć układ ładujący podłączony do systemu elektrycznego pojazdu.

## Safety requirements

1. Moduł B systemu ESAV nie może „przeciekać” prądu z akumulatorów.

## Derived requirements

1. Moduł B musi:
  1. monitorować poziom naładowania (napięcie) na baterii zasilającej,
  2. sygnalizować włączenie trybu awaryjnego zaświeceniem czerwonej diody LED,
  3. sygnalizować poprawne działanie zaświeceniem zielonej diody LED,
  4. sygnalizować oczekiwanie na odbiór danych okresowych od modułu A poprzez miganie pomarańczową diodą LED.
2. Komunikacja między modułami musi umożliwiać wymianę takich informacji:
  1. PING: wymiana danych co około sekundę (do weryfikacji istnienia połączenia),
  2. STOP: do wysłania danych w celu natychmiastowego przejścia modułu montowanego w samochodzie w tryb awaryjny,
  3. DATA: do wymiany informacji diagnostycznych (np. napięcie baterii).

# Project Design Description – specyfikacja projektu

## Hardware Design Description

### Moduł A

#### Sprzęt

- Raspberry Pi A+, karta SD
- WiFi dongle
- 3 diody LED, 3 rezystory ok. 150Ω
- Sterowanie stycznikiem ??? (stycznik: napięcie cewki >30V)
- układ step-up?
- Przycisk „Reset”
- układ włączający sprzężony z „kluczykiem”
- buzzer
- obudowa
- powerbank – albo akumulator

#### Podłączenie

### Moduł B

#### Sprzęt

- Raspberry Pi A+, karta SD
- WiFi dongle
- Przycisk „STOP” (grzybek?)
- ekran alfanumeryczny (?)
- obudowa
- powerbank

#### Podłączenie

## Software Design Description

## Requirements traceability matrix

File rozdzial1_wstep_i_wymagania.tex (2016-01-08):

\chapter{Wstęp}
\label{cha:wstep}

Laboratorium pojazdów autonomicznych AGH--Delphi ma za zadanie zbudowanie pojazdu autonomicznego na bazie udostępnionego pojazdu elektrycznego (zob. zdjęcie \ref{fig:electric_vehicle}). Podczas prac konieczne jest zapewnienie bezpieczeństwa podczas testowania algorytmów sterowania. Algorytmy takie mogą nie działać poprawnie, w~związku z~czym w~trakcie testów może zajść potrzeba awaryjnego przerwania jazdy samochodu.

\begin{figure}[h]
	\centering
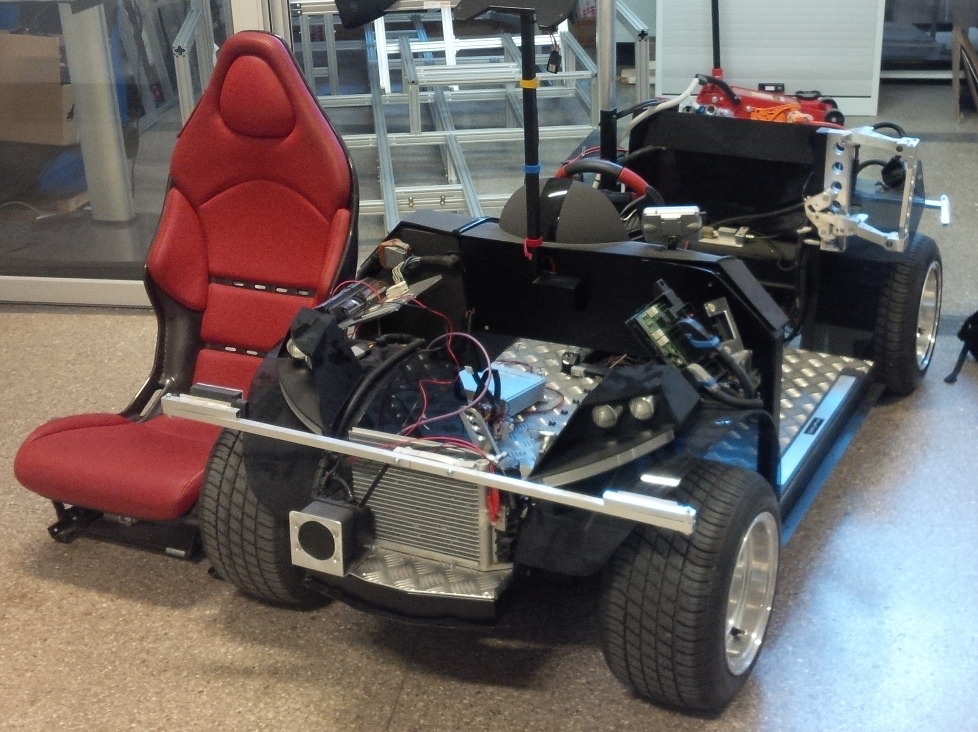
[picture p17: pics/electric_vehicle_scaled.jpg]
	
	\caption{\label{fig:electric_vehicle}Samochód elektryczny udostępniony przez firmę Delphi (zdjęcie: P. Banaszkiewicz).}
\end{figure}

Awaryjne przerwanie jazdy samochodu powinno odbyć się poprzez wyłączenie zasilania silnika samochodu. O ile jest to możliwe, należy uniknąć odłączenia zasilania reszty samochodu (np. układu kierowniczego lub komputera pokładowego).

%---------------------------------------------------------------------------

\section{Cele projektu}
\label{sec:cele_projektu}

System ESAV (ang. \textit{Emergency Stop Autonomous Vehicle} – zdalny wyłącznik bezpieczeństwa dla samochodu autonomicznego) powinien charakteryzować się następującymi właściwościami:

\begin{itemize}
\item Możliwość natychmiastowego zatrzymania pojazdu na polecenie operatora.
\item Natychmiastowe zatrzymanie pojazdu w przypadku utraty zasilania systemu ESAV.
\item Natychmiastowe zatrzymanie pojazdu w przypadku przerwania transmisji pomiędzy modułami systemu ESAV.
\item Natychmiastowe zatrzymanie pojazdu w przypadku zakłóceń pracy systemu ESAV (na przykład w wyniku błędów transmisji).
\item Możliwość poruszania się pojazdu tylko jeśli system ESAV jest zasilany.
\item Możliwość poruszania się pojazdu tylko w przypadku rozpoczęcia prawidłowej transmisji danych \item pomiędzy modułami systemu ESAV.
\item Możliwość wyświetlenia aktualnego stanu systemu ESAV.
\end{itemize}

W niniejszym opisie projektu używane będą następujące pojęcia skrótowe:
\begin{itemize}
\item \textbf{moduł A}: bazowy moduł systemu ESAV; to z niego korzysta operator aby wyłączyć zasilanie silnika w samochodzie,
\item \textbf{moduł B}: moduł montowany w samochodzie, który odpowiedzialny jest za wyłączenie zasilania silnika,
\item \textbf{tryb awaryjny}: tryb modułu B w którym następuje odłączenie zasilania silnika samochodu.
\end{itemize}

Zasilanie obydwu modułów powinno być całkowicie niezależne od zasilania pojazdu, a wymianę akumulatorów łatwa. Ponadto obydwa moduły muszą monitorować i pokazywać poziom naładowania swoich akumulatorów.

Po wyłączeniu pojazdu przez system ESAV układ musi zostać przywrócony do pracy poprzez zresetowanie.

System ESAV powinien być systemem bezobsługowym: raz skonfigurowany ma poprawnie pracować bez ingerencji użytkownika. Budowa systemu powinna umożliwiać innym osobom kontynuowanie prac nad nim. W tym celu jego oprogramowanie powinno być otwarto-źródłowe, a sprzęt wymienialny.

%---------------------------------------------------------------------------

\section{Wymagania funkcjonalne}
\label{sec:wymagania_funkcjonalne}

Na podstawie opisu z rozdziału \ref{sec:cele_projektu} wyznaczono poniższe cele funkcjonalne systemu ESAV:

\begin{enumerate}[label=\thesection.\arabic{*}.,leftmargin=4em]
\item \label{wym_fun1} Moduł B przy braku zasilania ma odcinać zasilanie silnika samochodu.
\item \label{wym_fun2} Po włączeniu moduł B ma oczekiwać na dane aktywujące jego pracę, które ma otrzymać od modułu A. Stan modułu B sygnalizowany jest migającą czerwoną diodą.
\item \label{wym_fun3} Dopóki moduł B nie odbierze danych aktywujących, pojazd nie może się poruszać.
\item \label{wym_fun4} Po odebraniu danych aktywujących, moduł B powinien umożliwić jazdę samochodu. Stan modułu B sygnalizowany jest świecącą zieloną diodą.
\item \label{wym_fun5} Jeżeli podczas działania moduł B przestanie odbierać transmisję, musi on przejść w tryb awaryjny. Stan modułu sygnalizowany jest ciągle świecącą się czerwoną diodą.
\item \label{wym_fun6} Po naciśnięciu przycisku wyłączenia awaryjnego w module A przez operatora, moduł B musi przejść w tryb awaryjny. Stan modułu sygnalizowany jest ciągle świecącą się czerwoną diodą.
\item \label{wym_fun7} Po zresetowaniu modułu B poprzez naciśnięcie przycisku „Reset”, moduł B powraca z trybu awaryjnego do stanu oczekiwania na dane aktywujące. Stan modułu sygnalizowany jest migającą czerwoną diodą.
\item \label{wym_fun8} Po wyłączeniu zasilania modułu B musi nastąpić odłączenie zasilania silnika samochodu.
\item \label{wym_fun9} Bateria (akumulator) modułu B może być ładowana w trakcie ładowania akumulatorów pojazdu.
\end{enumerate}

%---------------------------------------------------------------------------

\section{Wymagania użytkowe}
\label{sec:wymagania_wydajnosciowe}

Na podstawie opisu z rozdziału \ref{sec:cele_projektu} wyznaczono poniższe cele zasięgu, czasu oraz szybkości działania systemu ESAV:

\begin{enumerate}[label=\thesection.\arabic{*}.,leftmargin=4em]
\item \label{wym_uzyt1} System ESAV musi pracować bez konieczności wymiany bądź ładowania baterii (akumulatorów) przez minimum 5 godzin.
\item \label{wym_uzyt2} System ESAV musi być w stanie co 1 sekundę odbierać i dekodować dane, a następnie je wysyłać.
\item \label{wym_uzyt3} System ESAV musi pracować poprawnie na dystansie 100 metrów w otwartej przestrzeni.
\item \label{wym_uzyt4} System ESAV musi pracować poprawnie w pomieszczeniach.
\end{enumerate}

%---------------------------------------------------------------------------

\section{Wymagania współdziałania}
\label{sec:wymagania_wspoldzialania}

Na podstawie opisu z rozdziału \ref{sec:cele_projektu} wyznaczono poniższe cele integracji systemu ESAV z innymi urządzeniami:

\begin{enumerate}[label=\thesection.\arabic{*}.,leftmargin=4em]
\item \label{wym_wsp1} Moduł B musi poprawnie wyłączać silnik samochodu.
\item \label{wym_wsp2} Moduł B powinien mieć układ ładujący podłączony do systemu elektrycznego pojazdu.
\end{enumerate}

%---------------------------------------------------------------------------

\section{Wymagania bezpieczeństwa}
\label{sec:wymagania_bezpieczenstwa}

Na podstawie opisu z rozdziału \ref{sec:cele_projektu} wyznaczono poniższe wymagania bezpieczeństwa przy korzystaniu z systemu ESAV:
\begin{enumerate}[label=\thesection.\arabic{*}.,leftmargin=4em]
\item \label{wym_bezp1} Moduł B systemu ESAV nie może doprowadzić do porażenia użytkownika prądem.
\item \label{wym_bezp2} Komunikacja pomiędzy modułami powinna zabezpieczać przed atakami powtórzenia poleceń operatora.
\item \label{wym_bezp3} Moduł B systemu ESAV nie może nagrzewać się powyżej temperatury \SI{50}{\celsius}.
\end{enumerate}

%---------------------------------------------------------------------------

\section{Wymagania pochodne}
\label{sec:wymagania_pochodne}

Wymagania, które nie zostały jawnie wspomniane w rozdziałach \ref{sec:wymagania_funkcjonalne}—\ref{sec:wymagania_bezpieczenstwa}, a wynikają albo z opisu projektu (rozdział \ref{sec:cele_projektu}), albo pojawiły się w momencie implementowania projektu, zostały opisane w tym rozdziale.

Moduł B musi:

\begin{enumerate}[label=\thesection.\arabic{*}.,leftmargin=4em]
\item \label{wym_poch1} monitorować poziom naładowania (napięcie) na baterii zasilającej,
\item \label{wym_poch2} sygnalizować włączenie trybu awaryjnego świeceniem czerwonej diody,
\item \label{wym_poch3} sygnalizować oczekiwanie na transmisję miganiem czerwonej diody,
\item \label{wym_poch4} sygnalizować poprawne działanie świeceniem zielonej diody.
\end{enumerate}

Moduł A musi:

\begin{enumerate}[label=\thesection.\arabic{*}.,leftmargin=4em]
\setcounter{enumi}{4}
\item \label{wym_poch5} monitorować poziom naładowania (napięcie) na baterii zasilającej,
\item \label{wym_poch6} sygnalizować wysyłanie informacji miganiem zielonej diody,
\item \label{wym_poch7} mieć małe wymiary (aby możliwe było trzymania go w dłoniach).
\end{enumerate}

Komunikacja między modułami powinna umożliwiać wymianę takich informacji:

\begin{enumerate}[label=\thesection.\arabic{*}.,leftmargin=4em]
\setcounter{enumi}{7}
\item \label{wym_poch8} PING: wymiana danych co około sekundę (do weryfikacji istnienia połączenia),
\item \label{wym_poch9} STOP: do wysłania danych w celu natychmiastowego przejścia modułu B w tryb awaryjny,
\item \label{wym_poch10} DATA: do wymiany danych diagnostycznych (np. napięcia baterii).
\end{enumerate}

%---------------------------------------------------------------------------

\section{Podsumowanie}
\label{sec:wstep_podsumowanie}

Podejście do projektu oparte o listę wymagań (ang. \textit{requirements-driven design} \cite{Hug10} albo \textit{feature-driven development} \cite{Goy08}) umożliwia sprecyzowanie niewielkich wymagań a priori, które pozwalają wykonawcy implementować funkcjonalności pojedyncze i skierowane na konkretne wymagania, a także śledzić spełnienie tych wymagań w formie prostej tabeli (zob. rozdział \ref{sec:zrealizowane_wymagania}).

W tym rozdziale zostały wyszczególnione wymagania według sugerowanego schematu z~\cite{Hug10}, jednakże w przypadku projektów stricte programistycznych schemat ten może wyglądać inaczej.

Skupienie się na wyszczególnieniu wymagań przed rozpoczęciem prac nad projektem znacząco ułatwiło jego tworzenie, m.in. poprzez eliminację luk w opisie funkcjonalnym systemu ESAV.

\begin{figure}[h]
	\centering
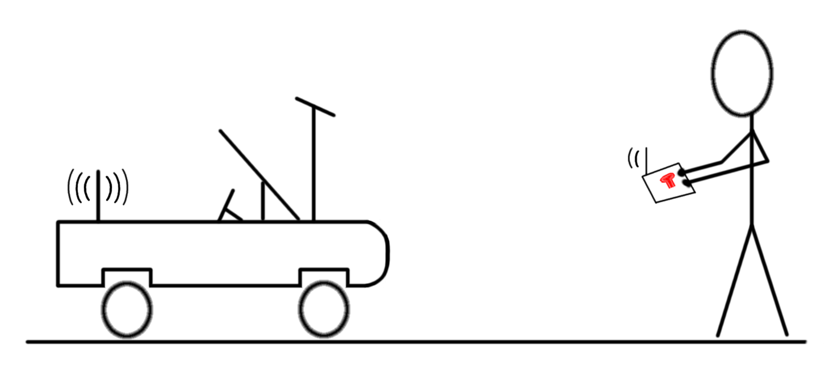
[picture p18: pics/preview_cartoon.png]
	
	\caption{\label{fig:preview}Rysunek poglądowy systemu w trakcie działania (rysenek: P. Banaszkiewicz).}
\end{figure}

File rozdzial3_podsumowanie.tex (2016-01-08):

\chapter{Podsumowanie projektu}
\label{cha:podsumowanie}

Celem niniejszej pracy inżynierskiej było stworzenie narzędzia ułatwiającego bezpieczne testowanie elektrycznego samochodu autonomicznego w laboratorium AGH--Delphi.

Za wkład własny w pracę uważam zrealizowanie następujących zagadnień:

\begin{itemize}
\item zebranie wymagań (któremu poświęcono prawie cały rozdział \ref{cha:wstep}),
\item stworzenie pierwszego prototypu systemu (nieopisanego w tej pracy, bazującego na architekturze Raspberry Pi i sieci WiFi),
\item opracowanie schematów logicznych oraz formatu komunikacji między modułami (\ref{subsec:schematy_cykli_dzialan}, \ref{subsec:format_pakietow}),
\item zbudowanie drugiego prototypu systemu, już przy wykorzystaniu platformy docelowej Arduino i~płytek wielostykowych do podłączenia elementów panelu operatora oraz modułów komunikacyjnych,
\item wykonanie kabla pozwalającego programować Arduino (\ref{subsec:kabel_do_programowania_arduino}),
\item zaimplementowanie algorytmów na podstawie opisanej logiki oraz komunikacji (\ref{subsec:maszyna_stanow}) i wgranie ich na Arduino,
\item przetestowanie poprawności działania algorytmów,
\item zbudowanie trwałych nakładek na platformy (\ref{subsec:obudowy}),
\item dobranie przekaźnika sterującego silnikiem (\ref{subsec:odlaczanie_zalaczanie_silnika}),
\item sprawdzenie, wraz z opiekunem pracy doktorem Markiem Długoszem, ilości wydzielanego ciepła przez przekaźnik pod obciążeniem (\ref{subsec:chlodzenie_SSR}).
\end{itemize}

Jak można odczytać z tabeli \ref{tab:spelnione_wymagania}, wszystkie wymagania zostały spełnione, a więc projekt zakończył się sukcesem.

Pomimo konieczności spełnienia dokładnie jednej funkcji (szybkiego wyłączenia samochodu w momencie zagrożenia), istnieją pewne możliwości dalszego rozwoju projektu. Po pierwsze można rozszerzyć jego działanie do dodatkowego hamowania pojazdu, które jest osiągalne poprzez przełączenie silnika w tryb generatora. Po drugie, można wykorzystać komunikację między modułami A i B do przesyłania informacji diagnostycznych samochodu do operatora, co w dalej umożliwiłoby użycie projektu jako swoistego zdalnego centrum diagnostycznego samochodu.

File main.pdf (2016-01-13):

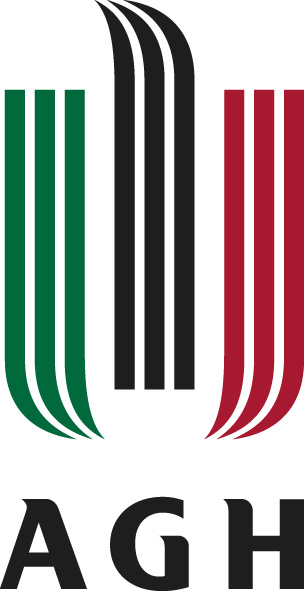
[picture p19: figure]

AKADEMIA GÓRNICZO-HUTNICZA IM. STANISŁAWA STASZICA W KRAKOWIE

WYDZIAŁ ELEKTROTECHNIKI, AUTOMATYKI, INFORMATYKI I INZYNIERII BIOMEDYCZNEJ ˙

KATEDRA AUTOMATYKI I INZYNIERII BIOMEDYCZNEJ ˙

## Praca dyplomowa inzynierska ˙

## Wył ącznik awaryjny pojazdu autonomicznego Emergency Stop Autonomous Vehicle

Autor: | Piotr Banaszkiewicz
Kierunek studiów: | Automatyka i Robotyka
Opiekun pracy: | dr inz. Marek Długosz ˙

Kraków, 2016

Uprzedzony o odpowiedzialnosci karnej na podstawie art. 115 ust. 1 i 2 ustawy ´ z dnia 4 lutego 1994 r. o prawie autorskim i prawach pokrewnych (t.j. Dz.U. z 2006 r. Nr 90, poz. 631 z późn. zm.): „Kto przywłaszcza sobie autorstwo albo wprowadza w bł ąd co do au-
torstwa całosci lub czę ´ | sci cudzego utworu albo artystycznego wykonania, podlega grzywnie, ´
karze ograniczenia wolnosci albo pozbawienia wolno ´ | sci do lat 3. Tej samej karze podlega, ´
kto rozpowszechnia bez podania nazwiska lub pseudonimu twórcy cudzy utwór w wersji oryginalnej albo w postaci opracowania, artystyczne wykonanie albo publicznie zniekształca taki utwór, artystyczne wykonanie, fonogram, wideogram lub nadanie.”, a takze uprzedzony o od- ˙ powiedzialnosci dyscyplinarnej na podstawie art. 211 ust. 1 ustawy z dnia 27 lipca 2005 r. ´ Prawo oszkolnictwie wyzszym (t.j. Dz. U. z 2012 r. poz. 572, z późn. zm.): „Za naruszenie prze- ˙ pisów obowi ązuj ących w uczelni oraz za czyny uchybiaj ące godnosci studenta student ponosi ´
odpowiedzialnosć dyscyplinarn ą przed komisj ą dyscyplinarn ą albo przed s ądem kole ´ | ze ńskim ˙
samorz ądu studenckiego”, oswiadczam, ´ | ze niniejsz ą pracę dyplomow ą wykonałem osobi ˙ | scie i ´
samodzielnie i ze nie korzystałem ze źródeł innych ni ˙ | z wymienione w pracy. ˙

### Serdecznie dziękuję opiekunowi pracy, Panu Doktorowi Markowi Długoszowi, a takze opiekunowi ˙ pracowni inzynierskiej, Panu Doktorowi Janu- ˙ szowi Tenecie, za niesion ą pomoc i zawsze dobr ą

radę.

## Spis tresci ´

1.3. | Wymagania uzytkowe | | 9 ˙
1.5. Wymagania bezpieczenstwa | 10 ´
2.1. Opis częsci sprzętowej | 13 ´
2.1.6. Schematy poł ączen | 17 ´
2.2. Opis częsci programowej | 20 ´
2.2.1. Schematy cykli-działan | 20 ´
2.3. Zakres zrealizowanych wymagan | 28 ´

### 6 SPIS TRESCI ´

P. Banaszkiewicz Wył ącznik awaryjny pojazdu autonomicznego

## 1. Wstęp

Laboratorium pojazdów autonomicznych AGH–Delphi ma za zadanie zbudowanie pojazdu autono-

micznego na bazie udostępnionego pojazdu elektrycznego (zob. zdjęcie 1.1). Podczas prac konieczne

jest zapewnienie bezpieczenstwa podczas testowania algorytmów sterowania. Algorytmy takie mog ą nie ´
działac poprawnie, w zwi ązku z czym w trakcie testów mo ´ | ze zaj ˙ | sć potrzeba awaryjnego przerwania ´

jazdy samochodu.


Fig. 1.1. Samochód elektryczny udostępniony przez firmę Delphi (zdjęcie: P. Banaszkiewicz).

Awaryjne przerwanie jazdy samochodu powinno odbyc się poprzez wył ączenie zasilania silnika sa- ´
mochodu. O ile jest to mozliwe, nale ˙ | zy unikn ą ˙ | c odł ączenia zasilania reszty samochodu (np. układu kie- ´

rowniczego lub komputera pokładowego).

8 1.1. Cele projektu

## 1.1. Cele projektu

System ESAV (ang. Emergency Stop Autonomous Vehicle – zdalny wył ącznik bezpieczenstwa dla ´

samochodu autonomicznego) powinien charakteryzowac się następuj ącymi wła ´ | sciwo ´ | sciami: ´
– Mozliwo ˙ | sć natychmiastowego zatrzymania pojazdu na polecenie operatora. ´

– Natychmiastowe zatrzymanie pojazdu w przypadku utraty zasilania systemu ESAV.

– Natychmiastowe zatrzymanie pojazdu w przypadku przerwania transmisji pomiędzy modułami

systemu ESAV.

– Natychmiastowe zatrzymanie pojazdu w przypadku zakłócen pracy systemu ESAV (na przykład ´

w wyniku błędów transmisji).

– Mozliwo ˙ | sć poruszania się pojazdu tylko je ´ | sli system ESAV jest zasilany. ´
– Mozliwo ˙ | sć poruszania się pojazdu tylko w przypadku rozpoczęcia prawidłowej transmisji danych ´

– pomiędzy modułami systemu ESAV.

– Mozliwo ˙ | sć wy ´ | swietlenia aktualnego stanu systemu ESAV. ´

W niniejszym opisie projektu uzywane będ ą następuj ące pojęcia skrótowe: ˙

– moduł A: bazowy moduł systemu ESAV; to z niego korzysta operator aby wył ączyc zasilanie ´

silnika w samochodzie,

– moduł B: moduł montowany w samochodzie, który odpowiedzialny jest za wył ączenie zasilania

silnika,

– tryb awaryjny: tryb modułu B w którym następuje odł ączenie zasilania silnika samochodu.

| Zasilanie obydwu modułów powinno byc całkowicie niezale ´ | zne od zasilania pojazdu, a wymianę ˙
akumulatorów łatwa. Ponadto obydwa moduły musz ą monitorowac i pokazywa ´ | c poziom naładowania ´

swoich akumulatorów.

Po wył ączeniu pojazdu przez system ESAV układ musi zostac przywrócony do pracy poprzez zrese- ´

towanie.

| System ESAV powinien byc systemem bezobsługowym: raz skonfigurowany ma poprawnie praco- ´
wac bez ingerencji u ´ | zytkownika. Budowa systemu powinna umo ˙ | zliwia ˙ | c innym osobom kontynuowanie ´

prac nad nim. W tym celu jego oprogramowanie powinno byc otwarto-źródłowe, a sprzęt wymienialny. ´

1.2. Wymagania funkcjonalne | 9

## 1.2. Wymagania funkcjonalne

Na podstawie opisu z rozdziału 1.1 wyznaczono ponizsze cele funkcjonalne systemu ESAV: ˙

1.2.1. Moduł B przy braku zasilania ma odcinac zasilanie silnika samochodu. ´
1.2.2. Po wł ączeniu moduł B ma oczekiwac na dane aktywuj ące jego pracę, które ma otrzyma ´ | c od ´

modułu A. Stan modułu B sygnalizowany jest migaj ąc ą czerwon ą diod ą.

1.2.3. Dopóki moduł B nie odbierze danych aktywuj ących, pojazd nie moze się porusza ˙ | c.´
1.2.4. Po odebraniu danych aktywuj ących, moduł B powinien umozliwi ˙ | c jazdę samochodu. Stan mo- ´

dułu B sygnalizowany jest swiec ąc ą zielon ą diod ą. ´

1.2.5. Jezeli podczas działania moduł B przestanie odbiera ˙ | c transmisję, musi on przej ´ | sć w tryb awa- ´

ryjny. Stan modułu sygnalizowany jest ci ągle swiec ąc ą się czerwon ą diod ą. ´

1.2.6. Po nacisnięciu przycisku wył ączenia awaryjnego w module A przez operatora, moduł B musi ´
przejsć w tryb awaryjny. Stan modułu sygnalizowany jest ci ągle ´ | swiec ąc ą się czerwon ą diod ą. ´
1.2.7. Po zresetowaniu modułu B poprzez nacisnięcie przycisku „Reset”, moduł B powraca z trybu ´

awaryjnego do stanu oczekiwania na dane aktywuj ące. Stan modułu sygnalizowany jest miga-

j ąc ą czerwon ą diod ą.

1.2.8. Po wył ączeniu zasilania modułu B musi nast ąpic odł ączenie zasilania silnika samochodu. ´
1.2.9. Bateria (akumulator) modułu B moze by ˙ c ładowana w trakcie ładowania akumulatorów po- ´

jazdu.

## 1.3. Wymagania uzytkowe ˙

Na podstawie opisu z rozdziału 1.1 wyznaczono ponizsze cele zasięgu, czasu oraz szybko ˙ | sci działa- ´

nia systemu ESAV:

1.3.1. System ESAV musi pracowac bez konieczno ´ | sci wymiany b ądź ładowania baterii (akumulato- ´

rów) przez minimum 5 godzin.

1.3.2. System ESAV musi byc w stanie co 1 sekundę odbiera ´ | c i dekodowa ´ | c dane, a następnie je ´

wysyłac.´

1.3.3. System ESAV musi pracowac poprawnie na dystansie 100 metrów w otwartej przestrzeni. ´
1.3.4. System ESAV musi pracowac poprawnie w pomieszczeniach. ´

10 1.4. Wymagania współdziałania

## 1.4. Wymagania współdziałania

Na podstawie opisu z rozdziału 1.1 wyznaczono ponizsze cele integracji systemu ESAV z innymi ˙

urz ądzeniami:

1.4.1. Moduł B musi poprawnie wył ączac silnik samochodu. ´
1.4.2. Moduł B powinien miec układ ładuj ący podł ączony do systemu elektrycznego pojazdu. ´

## 1.5. Wymagania bezpieczenstwa ´

Na podstawie opisu z rozdziału 1.1 wyznaczono ponizsze wymagania bezpiecze ˙ | nstwa przy korzy- ´

staniu z systemu ESAV:

1.5.1. Moduł B systemu ESAV nie moze doprowadzi ˙ | c do pora ´ | zenia u ˙ | zytkownika pr ądem. ˙
1.5.2. Komunikacja pomiędzy modułami powinna zabezpieczac przed atakami powtórzenia polece ´ | n´

operatora.

1.5.3. Moduł B systemu ESAV nie moze nagrzewa ˙ | c się powy ´ | zej temperatury ˙ | 50 ◦C.

## 1.6. Wymagania pochodne

Wymagania, które nie zostały jawnie wspomniane w rozdziałach 1.2—1.5, a wynikaj ą albo z opisu

projektu (rozdział 1.1), albo pojawiły się w momencie implementowania projektu, zostały opisane w tym

rozdziale.

Moduł B musi:

1.6.1. monitorowac poziom naładowania (napięcie) na baterii zasilaj ącej, ´
1.6.2. sygnalizowac wł ączenie trybu awaryjnego ´ | swieceniem czerwonej diody, ´
1.6.3. sygnalizowac oczekiwanie na transmisję miganiem czerwonej diody, ´
1.6.4. sygnalizowac poprawne działanie ´ | swieceniem zielonej diody. ´

Moduł A musi:

1.6.5. monitorowac poziom naładowania (napięcie) na baterii zasilaj ącej, ´
1.6.6. sygnalizowac wysyłanie informacji miganiem zielonej diody, ´
1.6.7. miec małe wymiary (aby mo ´ | zliwe było trzymania go w dłoniach). ˙
Komunikacja między modułami powinna umozliwia ˙ | c wymianę takich informacji: ´

1.7. Podsumowanie | 11
1.6.8. PING: wymiana danych co około sekundę (do weryfikacji istnienia poł ączenia),
1.6.9. STOP: do wysłania danych w celu natychmiastowego przejscia modułu B w tryb awaryjny, ´
1.6.10. DATA: do wymiany danych diagnostycznych (np. napięcia baterii).

## 1.7. Podsumowanie

Podejscie do projektu oparte o listę wymaga ´ | n (ang. ´ | requirements-driven design [1] albo feature-
driven development [2]) umozliwia sprecyzowanie niewielkich wymaga ˙ | n a priori, które pozwalaj ą wy- ´
konawcy implementowac funkcjonalno ´ | sci pojedyncze i skierowane na konkretne wymagania, a tak ´ | ze˙
sledzi ´ | c spełnienie tych wymaga ´ | n w formie prostej tabeli (zob. rozdział 2.3). ´

W tym rozdziale zostały wyszczególnione wymagania według sugerowanego schematu z [1], jed-
nakze w przypadku projektów stricte programistycznych schemat ten mo ˙ | ze wygl ąda ˙ | c inaczej. ´

Skupienie się na wyszczególnieniu wymagan przed rozpoczęciem prac nad projektem znacz ąco uła- ´

twiło jego tworzenie, m.in. poprzez eliminację luk w opisie funkcjonalnym systemu ESAV.

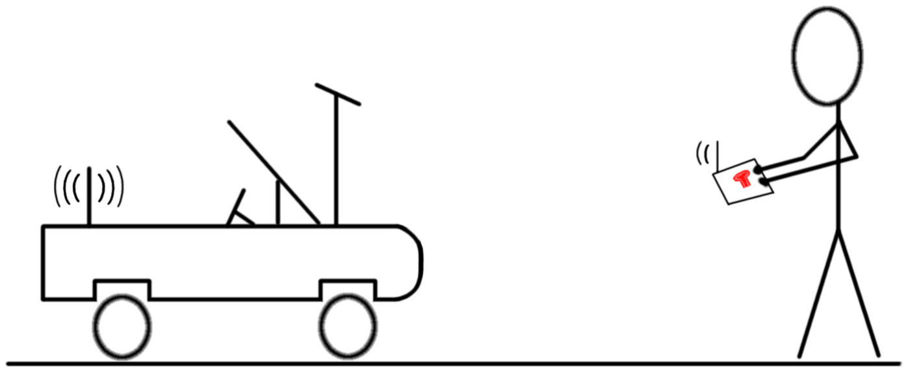
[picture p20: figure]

Fig. 1.2. Rysunek pogl ądowy systemu w trakcie działania (rysenek: P. Banaszkiewicz).

12 1.7. Podsumowanie

## 2. Wykonanie projektu

W tym rozdziale opisane zostało wykonanie projektu zgodnie z wymaganiami postawionymi w roz-

dziale 1.

## 2.1. Opis częsci sprzętowej ´

W ponizszym rozdziale została opisana platforma sprzętowa modułów A i B oraz ich współdziała- ˙

nie z innymi komponentami, m.in. z zasilaniem akumulatorowym czy z przekaźnikiem w samochodzie

elektrycznym.

### 2.1.1. Moduł A

Jest to moduł bazowy, tj. trzymany przez operatora w dłoni. Ze względu na uzycie Arduino Pro 328 ˙

5V 16MHz [3] (zob. zdjęcie 2.1) jako platformy sprzętowej, ma on niewielkie wymiary.


Fig. 2.1. Platforma sprzętowa Arduino Pro 328 5V 16MHz (zdjęcie: Piotr Banaszkiewicz).

14 2.1. Opis częsci sprzętowej ´

### 2.1.2. Moduł B

Jest to moduł, który został zamontowany w samochodzie. Jako platformę uzyte zostało ponownie ˙

Arduino Pro 328 5V 16MHz [3] (zob. zdjęcie 2.1). Podstawowa funkcja, tj. odł ączanie i zał ączanie

silnika elektrycznego, odbywa się za pomoc ą przekaźnika ASR-90DD-H firmy Anly Electronics (zob.

zdjęcie 2.2 i rozdział 2.1.7).


Fig. 2.2. Przekaźnik półprzewodnikowy ASR-90DD-H (zdjęcie: Piotr Banaszkiewicz).

### 2.1.3. Zasilanie

Obydwa moduły sprzętowe s ą zasilane z powerbanków Solo5 10000 mAh firmy Romoss. Posiadaj ą
one wbudowane rózne zabezpieczenia, m.in.: natę ˙ | zeniowe (dla zachowania ˙ | zywotno ˙ | sci), temperaturowe ´

czy zwarciowe (ang. short-circuit). Maj ą równiez układ, który wył ącza powerbank w sytuacji, gdy pr ąd ˙

ładowania jest bardzo niewielki [4].
Moduły A i B pobieraj ą bardzo niewiele pr ądu (zmierzone: między 20 mA a 50 mA), więc aby po-

wstrzymac powerbanki przed rozł ączaniem zwarto masę i źródło energii dwunastoma (w przypadku ´ modułu A) lub trzynastoma (w przypadku modułu B) rezystorami 910 Ω wpiętymi równolegle.

Poł ączenie równoległe takiej ilosci rezystorów daje do ´ | sć nisk ą rezystancję zastępcz ą (teoretycznie: ´
75,83 Ω dla modułu A, 70 Ω dla modułu B; praktycznie: występuj ą róznice w faktycznych warto ˙ | sciach ´

rezystancji rezystorów, zwłaszcza gdy te się nagrzej ą) i pozwala na obnizenie wydzielanego ciepła na ˙

rezystorach, co skutkuje:

– większym poborem pr ądu, dzięki czemu powerbanki się nie wył ączaj ą,

– nagrzewaniem rezystorów (z prawa Ohma: P =

U

2

R

=

(5.1)²

900

= 0.0289[W], gdzie 5,1 V to zmie-

rzone napięcie na rezystorze, a 900 Ω to przyblizona rezystancja nagrzanego rezystora), a więc w ˙

2.1. Opis częsci sprzętowej ´ | 15
przypadku 12 rezystorów połozonych bardzo blisko siebie mamy około ˙ | | 0,34 W wydzielanej mocy

w tym miejscu.

Ponadto banki energii umozliwiaj ą jednoczesne ładowanie jak i rozładowywanie, tzn. jest mo ˙ | zliwe ˙
wpięcie źródła zasilania na wejscie powerbanku, jak i obci ą ´ | zenia na jego wyj ˙ | scie. Dzięki temu power- ´
bank zasilaj ący moduł B mozna ładowa ˙ | c z portu USB znajduj ącego się w samochodzie. ´
Sama pojemnosć´ 10 000 mA h teoretycznie¹ pozwala na zasilanie układu pobieraj ącego 100 mA

przez 100 godzin lub układu pobieraj ącego 200 mA przez 50 godzin. Kazdy z modułów A i B po ob- ˙

ci ązeniu przez rezystory pobierał między ˙ | 100 a 200 mA. Poziom naładowania powerbanków mozna ˙

obserwowac na ich diodowych wskaźnikach. ´

### 2.1.4. Komunikacja

Do komunikacji wykorzystano parę modułów radiowych HC-12 433 MHz [5], które ł ącz ą się z plat-

formami sprzętowymi za pomoc ą ł ącza szeregowego. Prędkosć komunikacji takiego modułu w powie- ´

trzu wynosi 5000bps, czyli typowe pakiety przesyłane przez system (zob. rozdział 2.2.2), maj ące rozmiar

4B = 32b s ą przesyłane w ułamku sekundy.

Zasięg komunikacji modułów został przetestowany i wynosi 25 m w pomieszczeniu (przy braku scian ´

pomiędzy modułami) oraz 100 m na otwartej przestrzeni. Gdyby odległosci te były niewystarczaj ące, ´ HC-12 umozliwia podpięcie silniejszej zewnętrznej anteny [5] na zł ączu U.FL. ˙

### 2.1.5. Obudowy

Dla kazdego modułu systemu ESAV przygotowano sztywn ą nakładkę w formie płytki prototypowej ˙

(zdjęcia 2.3 i 2.4) z przylutowanymi komponentami wykorzystywanymi przez dany moduł. Zakładane

s ą one na górne i dolne piny modułów A i B (zob. zdjęcie 2.1).


Fig. 2.3. Nakładka na moduł A (zdjęcie: Piotr Banaszkiewicz).

Ponadto na kazd ą platformę została zaprojektowana obudowa. Na zdjęciu 2.1 wida ˙ | c cztery otwory w ´

platformie Arduino (dwa przy lewej krawędzi płytki PCB oraz dwa przy prawej krawędzi), które zostały
uzyte do przykręcenia ka ˙ | zdej z platform do obudowy. ˙
1W praktyce pojemnosć´ 10 000 mA h jest nieosi ągalna, gdyz powerbanki posiadaj ą mechanizmy wydłu ˙ | zaj ące ich ˙ | zywot- ˙

nosć; polega to na ładowaniu akumulatorów powerbanku tylko do pewnego stopnia. ´

16 2.1. Opis częsci sprzętowej ´


Fig. 2.4. Nakładka na moduł B (zdjęcie: Piotr Banaszkiewicz).

Obudowy bazuj ą na istniej ącym projekcie kontenerów dla Arduino Leonardo oraz Uno wykonanym

przez Zygmunta Wojcika [6]. Ich licencja zezwala na modyfikacje (więcej szczegółów dostępnych jest

pod adresem [7]).

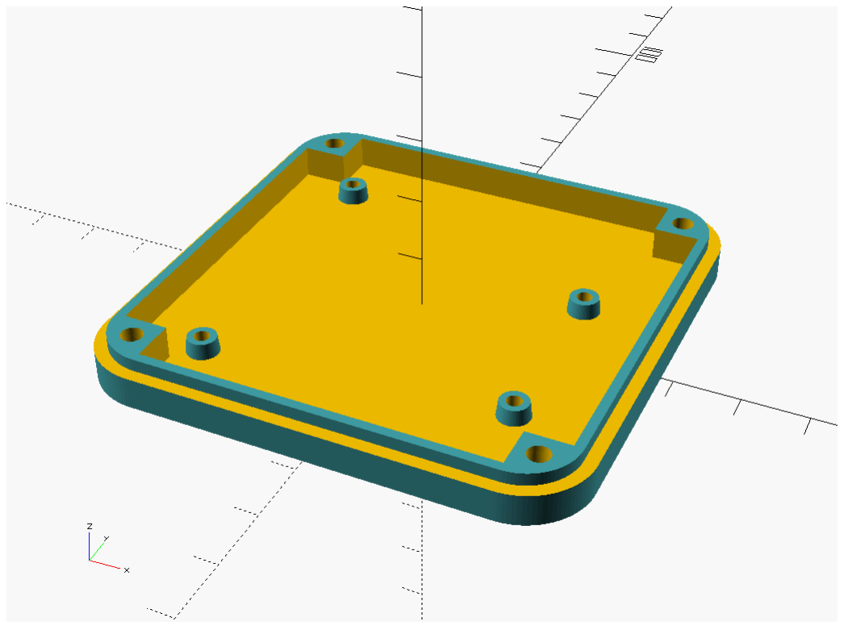
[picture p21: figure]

Fig. 2.5. Obudowa modułu A (oryginalny autor: Zygmunt Wojcik, modyfikacje: Piotr Banaszkiewicz [7]).

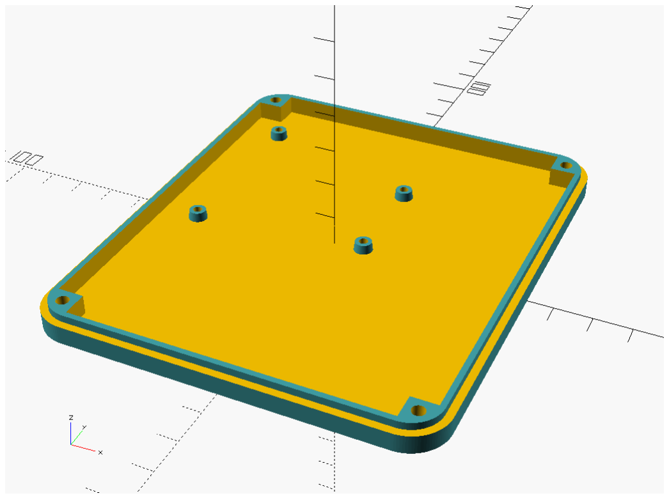
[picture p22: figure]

Fig. 2.6. Obudowa modułu B (oryginalny autor: Zygmunt Wojcik, modyfikacje: Piotr Banaszkiewicz [7]).

2.1. Opis częsci sprzętowej ´ | 17

### 2.1.6. Schematy poł ączen´

Symboliczny sposób poł ączenia modułu A, wejscia zasilaj ącego USB oraz transceivera radiowego ´

został przedstawiony na schemacie 2.7.


Fig. 2.7. Schemat poł ączen modułu A wygenerowany w programie Fritzing [8] (opra- ´ cowanie własne).

Bardzo podobnie wygl ąda symboliczny schemat poł ączen modułu B, z tym ´ | ze on dodatkowo steruje ˙

przekaźnikiem (schemat 2.8).

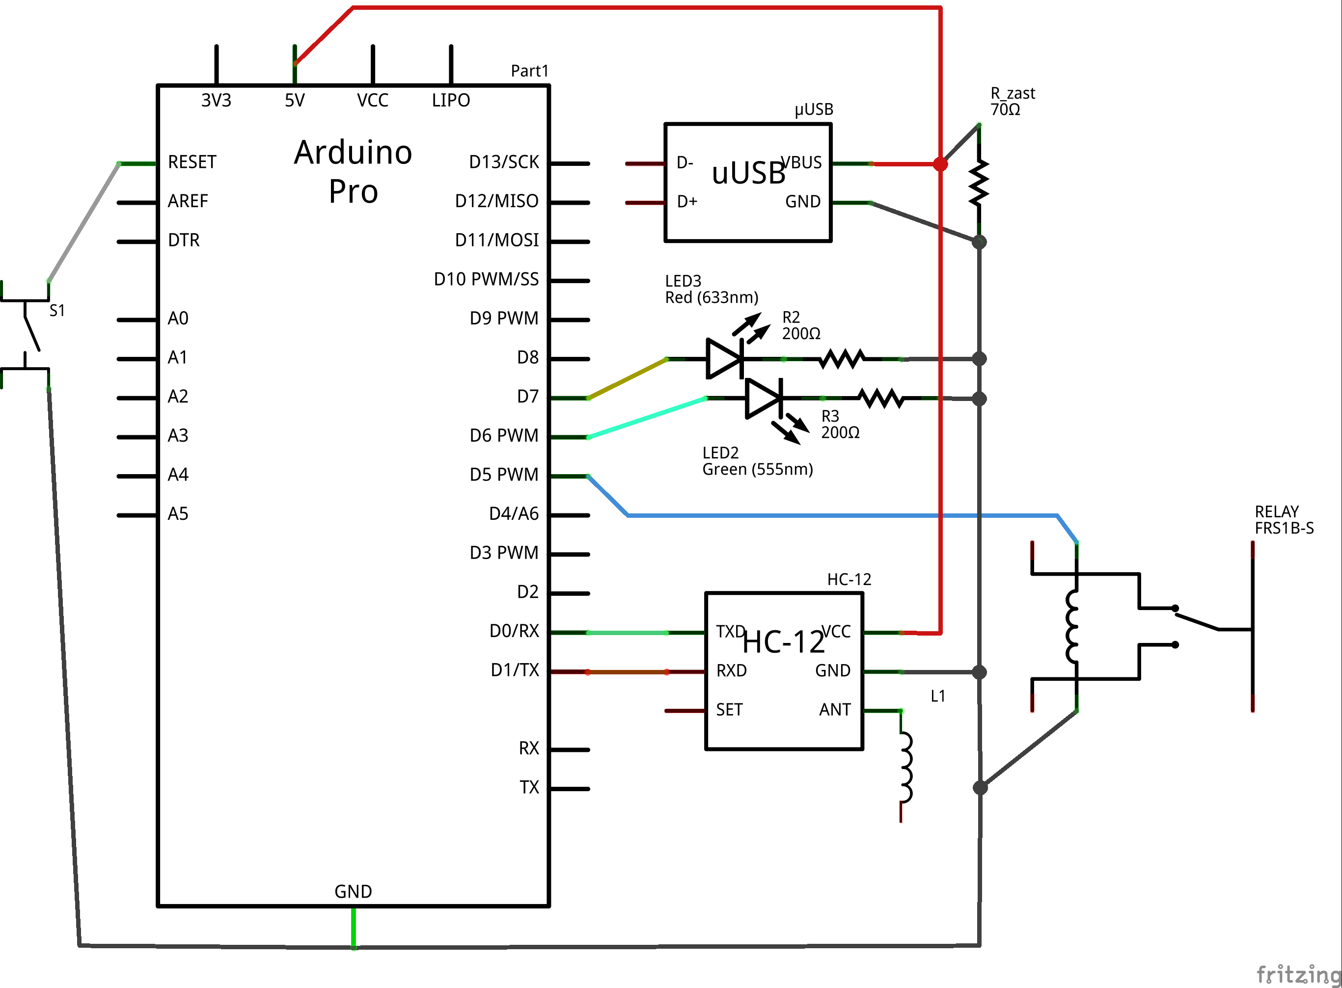
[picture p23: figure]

Fig. 2.8. Schemat poł ączen modułu B wygenerowany w programie Fritzing [8] (opra- ´ cowanie własne).

18 2.1. Opis częsci sprzętowej ´

### 2.1.7. Odł ączanie i zał ączanie silnika samochodu

Pomiędzy kabel zasilaj ący a moduł steruj ący prac ą silnika samochodu został wpięty przekaźnik

ASR-90DD-H (zob. zdjęcie 2.2). Moduł steruj ący odpowiedzialny jest za przetworzenie napięcia sta-

łego na pr ąd zmienny poprowadzony bezposrednio na uzwojenia silnika. ´

Przekaźnik ASR-90DD-H jest to przekaźnik półprzewodnikowy, a zatem typu Normally Open, sterowany napięciem stałym 3–32 V. Przekaźnik jest sterowany wyjsciem z modułu B (zob. element „RE- ´

LAY” na schemacie 2.8).
Według danych producenta, przekaźnik jest w stanie obsłuzy˙ c na wyj ´ | sciu mocy do ´ | 90 A pr ądu stałego
pod napięciem do 240 V. Wybrano przekaźnik mocno przekraczaj ący spodziewane natęzenie pr ądu, gdy ˙ | z˙

zapewnia to mniejsze wydzielanie ciepła (zob. rozdział 2.1.8).

Niestety producent nie udostępnia schematu elektrycznego przekaźnika w dokumentacji [9], więc
podczas jego montazu zadbano o kilka elementów bezpiecze ˙ | nstwa: ´

– zastosowano podkładkę silikonow ą jako izolator elektryczny,

– zastosowano radiator chłodz ący (widoczny na zdjęciu 2.9).


Fig. 2.9. Radiator chłodz ący przekaźnik SSR (zdjęcie: Piotr Banaszkiewicz).

Elementy te zgodne s ą z zaleceniami polskiego producenta przekaźników, firmy Relpol [10].

### 2.1.8. Chłodzenie przekaźnika półprzewodnikowego

Przekaźniki półprzewodnikowe z powodu pewnej niskiej opornosci własnej w momencie podł ączo- ´
nego wyjscia mocy wydzielaj ą du ´ | z ą ilo ˙ | sć energii w postaci ciepła. ´

W ramach pracy inzynierskiej przeprowadzono eksperyment polegaj ący na zmierzeniu temperatury ˙

obudowy działaj ącego przekaźnika podczas wł ączonego obci ązenia. ˙

2.1. Opis częsci sprzętowej ´ | 19

Przekaźnik został umieszczony na radiatorze i pracował przez kilka minut (do momentu ustalenia
się temperatury) pod stałym obci ązeniem. Kamera termowizyjna ostawiona była tak, by mierzy ˙ | c tem- ´

peraturę radiatora oraz obudowy przekaźnika. Tabela 2.1 zawiera zestawienie długosci czasu działania ´
przekaźnika pod obci ązeniem, a tak ˙ | ze uzyskanej na ko ˙ | ncu eksperymentu temperatury, natomiast zdjęcia ´

2.10 i 2.11 ukazuj ą obrazy z kamery termowizyjnej.

Tabela 2.1. Parametry eksperymentu obci ązenia przekaźnika półprzewodnikowego ˙

Czas obci ązenia | Napięcie | Natę ˙ | zenie | Temperatura radiatora ˙
a | Temperatura | obu-

dowy przekaźnikaa

8 min | 45 V | 36 A | 25 ◦C | ok. 60 ◦C
8 min | 42,5 V | 43 A | 25–35 ◦C | ok. 90 ◦C

a
pod koniec pomiaru


Fig. 2.10. Obraz uzyskany za pomoc ą kamery termowizyjnej na koniec trwania eksperymentu z mniejszym obci ązeniem (zdjęcie: Marek Długosz). ˙

20 2.2. Opis częsci programowej ´

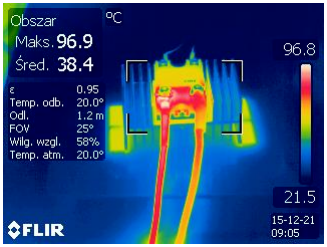
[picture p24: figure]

Fig. 2.11. Obraz uzyskany za pomoc ą kamery termowizyjnej na koniec trwania eksperymentu z większym obci ązeniem (zdjęcie: Marek Długosz). ˙

Na powyzszych zdjęciach najcieplejszym elementem była ˙ | sruba słu ´ | z ąca do przykręcenia kabla zasi- ˙
laj ącego. Temperatura ciepłego miejsca na obudowie przekaźnika była o około 15 ◦C nizsza; uwzględ- ˙

nione to zostało w tabeli 2.1 poprzez odjęcie ok. 10 ◦C od maksymalnej mierzonej temperatury.

Ponadto nalezy zauwa ˙ | zy˙ c jak niewiele nagrzewał się radiator, do którego przymocowany został prze- ´

kaźnik. To udowadnia, ze jest on wystarczaj ący dla zastosowania w samochodzie. ˙

Na samym koncu nale ´ | zy zauwa ˙ | zy˙ c,´ ze przekaźnik nie powinien by ˙ | c w realnych zastosowaniach ´
narazony na tak du ˙ | ze obci ą ˙ | zenia przez tak długi czas; według obserwacji, maksymalny pr ąd chwilowy ˙
w trakcie przyspieszania pojazdu i skręcania jednoczesnie wynosił około ´ | 50 A.

## 2.2. Opis częsci programowej ´

W tym rozdziale opisano m.in. logikę, algorytmy i struktury danych wykorzystywane przez pro-

gramy modułów A i B.

### 2.2.1. Schematy cykli-działan´

Ponizsze schematy reprezentuj ą logikę, zdarzenia oraz czynno ˙ | sci, jakimi posługuj ą się moduły A i B. ´

Dokładny opis pakietów danych oraz momenty, w których s ą przesyłane, znajduje się w rozdziale

2.2.2.

2.2. Opis częsci programowej ´ | 21


Fig. 2.12. Graf cykli-działan dla modułu A (opracowanie własne). ´

22 2.2. Opis częsci programowej ´


Fig. 2.13. Graf cykli-działan dla modułu B (opracowanie własne). ´

### 2.2.2. Format pakietów

Kazdy pakiet ma długo ˙ | sć 4 bajtów: ´

2.2. Opis częsci programowej ´ | 23

0x FC
|{z}
e
ABCD | {z }

c

00
|{z}
s

(2.1)

gdzie

e – bajt emergency. Jezeli jego warto ˙ | sć to ´ | 0xF F to moduł B ma natychmiast przejsć do trybu ´

awaryjnego. W praktyce oznacza to, ze operator wcisn ął przycisk „STOP” modułu A. ˙

c – 2 bajty zapisuj ące wartosć liczbow ą licznika modułu A (typ bez znaku, 16 bitów), ´

s – bajt stopu, jego wartosć zawsze ma by ´ | c równa ´ | 0x00.

Istniej ą 2 pakiety specjalne przesyłane między modułami A i B w celu synchronizacji i rozpoczęcia

działania:

– pakiet danych aktywacyjnych wysyłany przez moduł A: 0xFFFFFF00,

– pakiet odpowiedzi na dane aktywacyjne wysyłany przez moduł B: 0x11FFFF00,

– ponadto kazdy pakiet danych wysyłany przez moduł A ju ˙ | z po odebraniu odpowiedzi na dane ˙

aktywacyjne zawiera bajt emergency ustawiony na wartosć´ 0x22 – za wyj ątkiem sytuacji, w której
moduł A z ąda od modułu B przej ˙ | scia w tryb awaryjny; wtedy ten bajt ustawiony jest na warto ´ | sć´

0xFF.

Przykładowe pakiety:

– 0x223F0E00: moduł A wysyła informację o braku koniecznosci przej ´ | scia w tryb awaryjny oraz o ´

wartosci licznika (16142), ´

– 0xFFA37800: moduł A wysyła informację o przejsciu w tryb awaryjny oraz o ostatniej warto ´ | sci ´

licznika (41848).

### 2.2.3. Maszyna stanów

Oprogramowanie modułów A i B wykorzystuje proste maszyny stanów [11].

Stany modułu A:

1. CONNECTING: wysyłanie pakietu danych aktywacyjnych co 1 sekundę, oczekiwanie na odpo-

wiedź,

2. PING: wysyłanie obecnej wartosci licznika co 1 sekundę, zwiększanie warto ´ | sci licznika, ´
3. STOP: wysyłanie ostatniej wartosci licznika oraz ustawionego bajtu ´ | emergency co 0,5 sekundy.

Stany modułu B:

1. WAIT: oczekiwanie na przyjscie pakietu danych aktywacyjnych; odesłanie na niego odpowiedzi, ´

24 2.2. Opis częsci programowej ´

2. RUN: zwiększanie wewnętrznego licznika, odbieranie wartosci licznika modułu A, porównywanie ´

obu liczników, sprawdzanie bajtu emergency,

3. STOP: podtrzymywanie wył ączenia zasilania.

Warunki przejscia między stanami modułu A: ´

– CONNECTING → PING: gdy pakiet odpowiedzi na dane aktywacyjne wysłany przez moduł B to

0x11FFFF00,

– PING → STOP: gdy operator wcisnie przycisk „RESET”. ´

Warunki przejscia między stanami modułu B: ´

– WAIT → RUN: gdy pakiet danych aktywuj ących wysłany przez moduł A to 0xFFFFFF00,

– RUN → STOP: gdy jeden z warunków jest spełniony:

– bajt emergency w przychodz ącym pakiecie ma wartosć´ 0xFF,

– licznik wewnętrzny ma wartosć ró ´ | zn ą od warto ˙ | sci licznika wysłanej przez moduł A w przy- ´

chodz ącym pakiecie,

– przez 3 sekundy nie nadeszły zadne dane od modułu A. ˙

### 2.2.4. Panel operatorski

Obydwa moduły systemu ESAV zawieraj ą minimalny interfejs dla uzytkownika. Składa się on od- ˙

powiednio z:

– dla modułu A:

– przycisk „STOP” wywołuj ący przerwanie wewnętrzne platformy Arduino i w konsekwencji

wysłanie polecenia przejscia do trybu awaryjnego, ´

– przycisk „RESET” do łatwiejszego restartu urz ądzenia,

– zielon ą diodę informuj ąc ą o wysyłaniu danych przez port szeregowy,

– zółt ą diodę wł ączaj ąc ą się w momencie naci ˙ | snięcia przycisku „STOP” (spełnia ona funkcję ´
wizualnego sprzęzenia zwrotnego dla u ˙ | zytkownika), ˙

– dla modułu B:

– przycisk „RESET” do łatwiejszego restartu urz ądzenia,

– zielon ą diodę informuj ąc ą o poprawnym trybie pracy (stan „RUN”),

– czerwon ą diodę informuj ąc ą o oczekiwaniu na dane wejsciowe (szybka pulsacja) lub o przej- ´

sciu w tryb awaryjny (ci ągłe ´ | swiecenie). ´

2.2. Opis częsci programowej ´ | 25

### 2.2.5. Szyfrowanie komunikacji

Komunikacja pomiędzy modułami (za wyj ątkiem przekazywanych danych aktywacyjnych i odpo-

wiedzi na nie) jest w prosty sposób szyfrowana.
Do szyfrowania wykorzystywane s ą dwie tablice, kazda o długo ˙ | sci 256, co odpowiada ilo ´ | sci warto ´ | sci ´

pojedynczego bajtu. Szyfrowanie pojedynczego bajtu polega na odszukaniu w tablicy szyfruj ącej odpo-

wiadaj ącej mu wartosci zaszyfrowanej, a odszyfrowanie polega na odszukaniu w tablicy deszyfruj ącej ´

wartosci oryginalnej odpowiadaj ącej warto ´ | sci zaszyfrowanej. ´
Ponizszy przykład ilustruje szyfrowanie i deszyfrowanie na przykładzie czterech warto ˙ | sci: ´

Listing 2.1. Pseudokod zblizony do C pokazuj ący zasadę szyfrowania i deszyfrowania ˙

komunikacji systemu ESAV.

byte cipher_array[] = {3, 1, 0, 2};

byte decipher_array[] = {2, 1, 3, 0};

byte original = 2;

byte encrypted = cipher_array[original];

assert(original == decipher_array[encrypted]);

Dzięki wykorzystaniu tej prostej metody nie nast ąpił zaden narzut w wielko ˙ | sci przesyłanych pakie- ´
tów, niestety skutkiem słabszego bezpieczenstwa ni ´ | z w przypadku stosowania np. algorytmu AES [12]. ˙

### 2.2.6. Programowanie Arduino

Platforma Arduino, na której oparty jest system ESAV, programowana jest w srodowisku Arduino ´ IDE (zob. 2.14) za pomoc ą języka bardzo zblizonego do C. Opis jego składni, udostępnionych funkcji i ˙

klas dostępny jest w [13].

Podczas pracy nad projektem stworzono dwa pliki źródłowe, odpowiednio dla modułu A oraz B, a takze jedn ą bibliotekę w C++ współdzielon ą przez oba projekty, której zadaniem jest obsługiwanie ˙

szyfrowania i deszyfrowania komunikacji pomiędzy modułami.

Pliki źródłowe dostępne s ą w serwisie GitHub [14].

26 2.2. Opis częsci programowej ´


Fig. 2.14. Interfejs programu Arduino IDE uzywany do programowania na platformę ˙

Arduino (zdjęcie: Piotr Banaszkiewicz).

### 2.2.7. Kabel do programowania Arduino

Platforma Arduino Pro, w przeciwienstwie do innych większych mikrokontrolerów Arduino, nie za- ´

wiera programatora na USB. Programowanie Arduino Pro odbywa się poprzez port szeregowy (6 pinów

usytuowanych równolegle do płytki PCB, widocznych po lewej stronie na zdjęciu 2.1).


Fig. 2.15. Opis wyjsć u ´ zywanego konwertera USB-UART (zdjęcie: Botland [15]). ˙

2.2. Opis częsci programowej ´ | 27

Niestety uzywany konwerter USB-UART posiada zgodne wyprowadzenia (zob. 2.15), ale w nieod- ˙

powiedniej kolejnosci, co zostało przedstawione w tabeli 2.2. ´

Tabela 2.2. Zł ącza komunikacji szeregowej i zasilania platformy Arduino Pro oraz uzywanego konwertera USB-UART. ˙

Wyprowadzenie Arduino Pro | Wyprowadzenie konwertera USB-UART
RST | GND
TX | TXD
RX | RXD
5V | RTS
GND | CTS
GND | PWR

Podł ączenia wymagane do prawidłowego zaprogramowania Arduino Pro:

– RST → RTS

– TX → RXD

– RX → TXD

– 5V → PWR

– GND → GND

W zwi ązku z tym konieczne stało się stworzenie kabla pozwalaj ącego łatwo programowac moduły ´

systemu ESAV. Został on zbudowany na podstawie tzw. skrętki ethernetowej (zdjęcie 2.16).


Fig. 2.16. Zdjęcie kabla wykorzystywanego do programowania Arduino (zdjęcie: Piotr Banaszkiewicz).

28 2.3. Zakres zrealizowanych wymagan´

## 2.3. Zakres zrealizowanych wymagan´

W ponizszej tabeli zestawiono zało ˙ | zenia projektu wyszczególnione w rozdziale wraz z informacj ą ˙

o ich spełnieniu (b ądź wytłumaczeniem dlaczego nie zostały spełnione) oraz odnosnikiem do rozdziału ´

zawieraj ącego bardziej szczegółowe informacje na temat danej funkcjonalnosci. ´

Tabela 2.3. Macierz sledzenia wymaga ´ | n (ang. ´ | requirements traceability matrix [1]).

Numer wyma-

gania

Wymagane? | Spełnione? | Jak? | Roz.
1.2.1. | Tak | Tak | Przekaźnik typu Normally Open. | 2.1.7
1.2.2. | Tak | Tak | Oprogramowanie modułów A i B. | 2.2.1
1.2.3. | Tak | Tak | Przekaźnik typu Normally Open oraz oprogramowanie modułu B. | 2.2.3
1.2.4. | Tak | Tak | Oprogramowanie modułu B. | 2.2.3
1.2.5. | Tak | Tak | Oprogramowanie modułu B. | 2.2.3
1.2.6. | Tak | Tak | Oprogramowanie modułów A i B. | 2.2.3
1.2.7. | Tak | Tak | Podpięcie przycisku „RESET” do pinu RESET modułu B. | 2.2.4
1.2.8. | Tak | Tak | Przekaźnik typu Normally Open. | 2.1.7
1.2.9. | Nie | Nie | Zakupione powerbanki umozliwiaj ą ˙
| | | ładowanie podczas uzywania ich, ˙
jednakze to w gestii u ˙ | zytkownika ˙
jest korzystanie z tej mozliwo ˙ | sci. ´
| | | | 2.1.3
1.3.1. | Tak | Tak | Powerbanki powinny teoretycznie
zapewnic zasilanie przez około ´ | 50–
| | | 100 godzin.

2.1.3

1.3.2. | Tak | Tak | Prędkosć przesyłania danych mię- ´
dzy | modułami | HC-12 | wynosi

5000bps.

2.1.4

1.3.3. | Tak | Tak | Zasięg 100 m na otwartej prze-
| | | strzeni.

2.1.4

1.3.4. | Tak | Tak | Zasięg 25 m w pomieszczeniach
| | | (przy braku scian pomiędzy modu- ´
| | | łami).

2.1.4

1.4.1. | Tak | Tak | Moduł B odł ącza zasilanie modułu,
| | | który bezposrednio zasila silnik sa- ´
| | | mochodu.

2.1.7

2.3. Zakres zrealizowanych wymagan´ | 29
1.4.2. | Nie | Nie | Zakupione powerbanki umozliwiaj ą ˙
| | | ładowanie podczas uzywania ich, ˙
jednakze to w gestii u ˙ | zytkownika ˙
jest korzystanie z tej mozliwo ˙ | sci. ´

2.1.3

1.5.1. | Tak | Tak | Wejscie sterowania przekaźnika jest ´
| | | optoizolowane.

2.1.7

1.5.2. | Tak | Tak | Komunikacja pomiędzy modułami
| | | polega na wymianie szyfrowanego
| | | licznika.

2.2.5

1.5.3. | Tak | Tak | Przekaźnik dopiero wystawiony na
| | | bardzo długie działanie pod wy-
sokim obci ązeniem mo ˙ | ze osi ągn ą ˙ | c´
| | | temperaturę 100 ◦C.

2.1.8

1.6.1. | Nie | Nie | Poziom naładowania jest wyswie- ´
| | | tlany na obudowie powerbanku,
| | | więc nie ma koniecznosci dodatko- ´
| | | wego monitorowania przez moduł
| | | B.

2.1.3

1.6.2. | Tak | Tak | Spełnione dosłownie. | 2.2.4
1.6.3. | Tak | Tak | Spełnione dosłownie. | 2.2.4
1.6.4. | Tak | Tak | Spełnione dosłownie. | 2.2.4
1.6.5. | Nie | Nie | Poziom naładowania jest wyswie- ´ tlany na obudowie powerbanku, więc nie ma koniecznosci dodatko- ´ wego monitorowania przez moduł B. | 2.1.3
1.6.6. | Tak | Tak | Spełnione dosłownie. | 2.2.4
1.6.7. | Tak | Tak | Spełnione dosłownie. | 2.1.5
1.6.8. | Tak | Tak | Wysłanie pakietu danych jest rozu- miane jako „PING”. | 2.2.2
1.6.9. | Tak | Tak | Opisane w formacie pakietów. | 2.2.2
1.6.10. | Nie | Nie | Niewymagane.

30 2.4. Podsumowanie

## 2.4. Podsumowanie

Wykonanie projektu zostało podzielone na dwie częsci: czę ´ | sć zwi ązan ą stricte ze sprzętem oraz czę ´ | sć´
zwi ązan ą z programowaniem. Umozliwiło to zrównoleglenie pracy: w momencie oczekiwania na sprzęt ˙

rozwijana było oprogramowanie systemu ESAV.
Dzięki opisaniu wszystkich wymagan w rozdziale 1, mo ´ | zliwe zostało uło ˙ | zenie tabeli 2.3, która od ˙

razu pokazuje w jakim stanie ukonczenia jest projekt. ´

## 3. Podsumowanie projektu

Celem niniejszej pracy inzynierskiej było stworzenie narzędzia ułatwiaj ącego bezpieczne testowanie ˙

elektrycznego samochodu autonomicznego w laboratorium AGH–Delphi.
Za wkład własny w pracę uwazam zrealizowanie następuj ących zagadnie ˙ | n:´
– zebranie wymagan (któremu po ´ | swięcono prawie cały rozdział 1), ´

– stworzenie pierwszego prototypu systemu (nieopisanego w tej pracy, bazuj ącego na architekturze

Raspberry Pi i sieci WiFi),

– opracowanie schematów logicznych oraz formatu komunikacji między modułami (2.2.1, 2.2.2),

– zbudowanie drugiego prototypu systemu, juz przy wykorzystaniu platformy docelowej Arduino ˙

i płytek wielostykowych do podł ączenia elementów panelu operatora oraz modułów komunika-

cyjnych,

– wykonanie kabla pozwalaj ącego programowac Arduino (2.2.7), ´

– zaimplementowanie algorytmów na podstawie opisanej logiki oraz komunikacji (2.2.3) i wgranie

ich na Arduino,

– przetestowanie poprawnosci działania algorytmów, ´

– zbudowanie trwałych nakładek na platformy (2.1.5),

– dobranie przekaźnika steruj ącego silnikiem (2.1.7),

– sprawdzenie, wraz z opiekunem pracy doktorem Markiem Długoszem, ilosci wydzielanego ciepła ´ przez przekaźnik pod obci ązeniem (2.1.8). ˙

Jak mozna odczyta ˙ | c z tabeli 2.3, wszystkie wymagania zostały spełnione, a więc projekt zako ´ | nczył ´

się sukcesem.

Pomimo koniecznosci spełnienia dokładnie jednej funkcji (szybkiego wył ączenia samochodu w mo- ´
mencie zagrozenia), istniej ą pewne mo ˙ | zliwo ˙ | sci dalszego rozwoju projektu. Po pierwsze mo ´ | zna rozsze- ˙

rzyc jego działanie do dodatkowego hamowania pojazdu, które jest osi ągalne poprzez przeł ączenie sil- ´
nika w tryb generatora. Po drugie, mozna wykorzysta ˙ | c komunikację między modułami A i B do prze- ´

32

syłania informacji diagnostycznych samochodu do operatora, co w dalej umozliwiłoby u ˙ | zycie projektu ˙

jako swoistego zdalnego centrum diagnostycznego samochodu.

## Bibliografia

[1] J. M. Hughes. Real World Instrumentation with Python. O’Reilly Media, Inc., 2010. Chap. 8.
[2] S. Goyal. Major Seminar On Feature Driven Development. 2008. URL: http :// csis. pace.edu/

~marchese/CS616/Agile/FDD/fdd.pdf (http://csis.pace.edu/~marchese/CS616/Agile/FDD/fdd.pdf) .

[3] Arduino - ArduinoProBoard. URL: https://www.arduino.cc/en/Main/ArduinoBoardPro.
[4] Romoss - solo 5. URL: http:// romoss.com/ proview.php?ID=17. (http://romoss.com/proview.php?ID=17)
[5] HC-12 Wireless Serial Port Communication Module, User Manual v1.18. URL: https:// botland.

com.pl/index.php?controller=attachment&id_attachment=1188. (https://botland.com.pl/index.php?controller=attachment&id_attachment=1188)

[6] Z. Wojcik. 3D Printed Case for Arduino Uno, Leonardo. by ZygmuntW. 2015. URL: http:// www.

thingiverse.com/thing:628929.

[7] P. Banaszkiewicz. Module cases. 2015. URL: https:// github.com/ pbanaszkiewicz/ engineering-

thesis/tree/master/cases/README.md. (https://github.com/pbanaszkiewicz/engineering-thesis/tree/master/cases/README.md)

[8] Fritzing. URL: http://fritzing.org/ home/. (http://fritzing.org/home/)
[9] Anly Electronics ASR-90DD-H datasheet. URL: http:// www.anly.com.cn/ english/ pdf/ ASR_KB.

pdf (http://www.anly.com.cn/english/pdf/ASR_KB.pdf) .

[10] Przekaźniki półprzewodnikowe. URL: https:// www.relpol.pl/ content/ download/ 37247/ 517211/

file/techpol.pdf (https://www.relpol.pl/content/download/37247/517211/file/techpol.pdf) .

[11] J. Bromirski. Teoria automatów. Wydawnictwa Naukowo-Techniczne, 1969. Rozd. 4.4.3.1.
S. 181.
[12] The Twofish Team’s Final Comments on AES Selection. 2000. URL: http :// www.schneier.com/

paper-twofish-final.pdf (http://www.schneier.com/paper-twofish-final.pdf) .

[13] Arduino - Reference. URL: https://www.arduino.cc/en/Reference/HomePage.
[14] P. Banaszkiewicz. Engineering thesis. URL: https :// github. com/ pbanaszkiewicz/ engineering -

thesis. (https://github.com/pbanaszkiewicz/engineering-thesis)

[15] Konwerter USB-UART FTDI 3,3/5V. URL: http:// botland.com.pl/ konwertery- usb- uart- rs232-

rs485/ 1611-konwerter-usb-uart-ft232-33-5v.html. (http://botland.com.pl/konwertery-usb-uart-rs232-rs485/1611-konwerter-usb-uart-ft232-33-5v.html)

# Spis rysunków

1.1 Samochód elektryczny udostępniony przez firmę Delphi (zdjęcie: P. Banaszkiewicz). . . | 7
1.2 Rysunek pogl ądowy systemu w trakcie działania (rysenek: P. Banaszkiewicz) | | 11
2.1 Platforma sprzętowa Arduino Pro 328 5V 16MHz (zdjęcie: Piotr Banaszkiewicz) | | 13
2.2 Przekaźnik półprzewodnikowy ASR-90DD-H (zdjęcie: Piotr Banaszkiewicz) | | 14
2.3 Nakładka na moduł A (zdjęcie: Piotr Banaszkiewicz) | | 15
2.4 Nakładka na moduł B (zdjęcie: Piotr Banaszkiewicz) | | 16

2.5 Obudowa modułu A (oryginalny autor: Zygmunt Wojcik, modyfikacje: Piotr Banaszkie-

wicz [7]) | 16

2.6 Obudowa modułu B (oryginalny autor: Zygmunt Wojcik, modyfikacje: Piotr Banaszkie-

wicz [7]) | 16

2.7 Schemat poł ączen modułu A wygenerowany w programie Fritzing [8] (opracowanie wła- ´

sne) | 17

2.8 Schemat poł ączen modułu B wygenerowany w programie Fritzing [8] (opracowanie wła- ´

sne) | | 17
2.9 Radiator chłodz ący przekaźnik SSR (zdjęcie: Piotr Banaszkiewicz) | | 18

2.10 Obraz uzyskany za pomoc ą kamery termowizyjnej na koniec trwania eksperymentu z
mniejszym obci ązeniem (zdjęcie: Marek Długosz) | 19 ˙

2.11 Obraz uzyskany za pomoc ą kamery termowizyjnej na koniec trwania eksperymentu z
większym obci ązeniem (zdjęcie: Marek Długosz) | | 20 ˙
2.12 Graf cykli-działan dla modułu A (opracowanie własne) | | 21 ´
2.13 Graf cykli-działan dla modułu B (opracowanie własne) | | 22 ´

2.14 Interfejs programu Arduino IDE uzywany do programowania na platformę Arduino ˙

(zdjęcie: Piotr Banaszkiewicz) | | 26
2.15 Opis wyjsć u ´ zywanego konwertera USB-UART (zdjęcie: Botland [15]) | | 26 ˙

2.16 Zdjęcie kabla wykorzystywanego do programowania Arduino (zdjęcie: Piotr Banaszkie-

wicz) | 27

SPIS TABLIC | 35

# Spis tablic

2.1 Parametry eksperymentu obci ązenia przekaźnika półprzewodnikowego | 19 ˙

2.2 Zł ącza komunikacji szeregowej i zasilania platformy Arduino Pro oraz uzywanego kon- ˙

wertera USB-UART | | 27
2.3 Macierz sledzenia wymaga ´ | n (ang. ´ | requirements traceability matrix [1]) | | 28

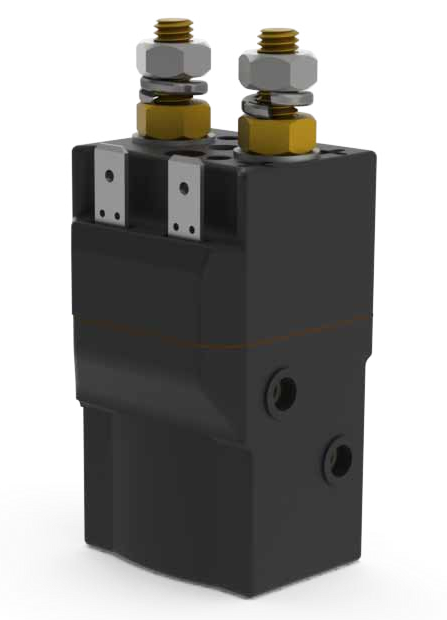
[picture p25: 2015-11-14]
pics/albright_SW60.png

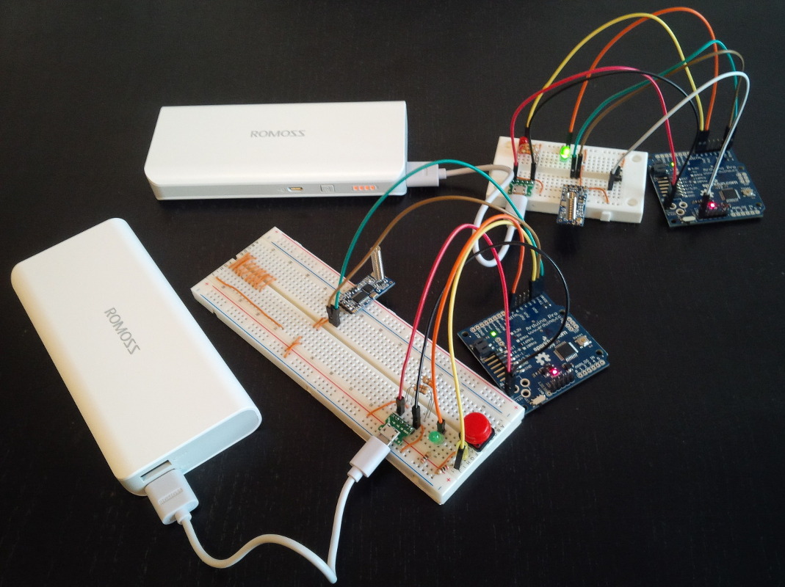
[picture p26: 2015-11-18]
pics/prototype.jpg

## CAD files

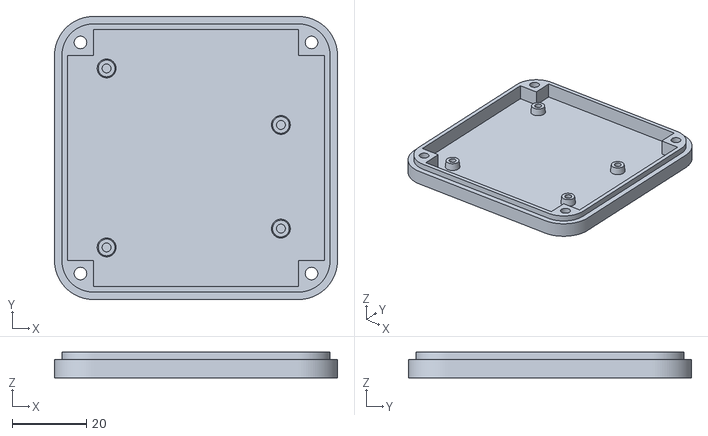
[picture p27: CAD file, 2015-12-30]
cases/containerA.stl
76.3 x 76.3 x 7.00

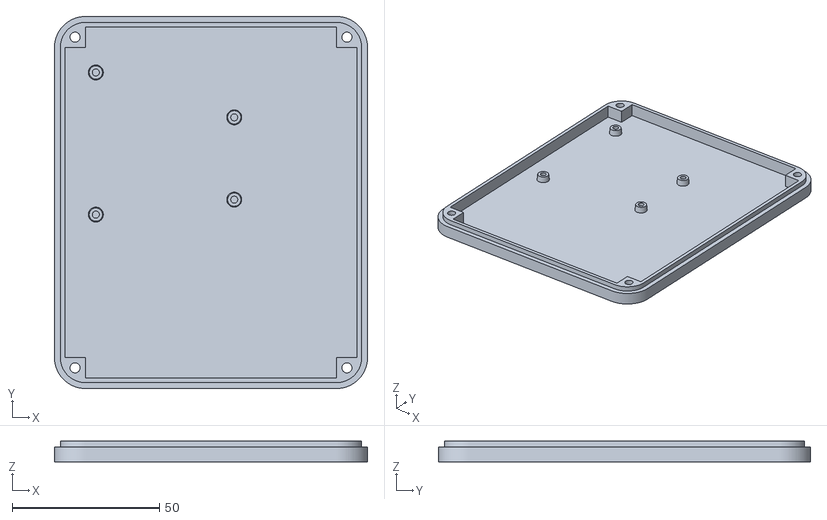
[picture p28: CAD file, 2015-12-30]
cases/containerB.stl
106.3 x 126.3 x 7.00

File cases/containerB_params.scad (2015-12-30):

//  ----------------------------------------------------------------------- LICENSE
//  This "3D Printed Case for Arduino Uno, Leonardo" by Zygmunt Wojcik is licensed
//  under the Creative Commons Attribution-ShareAlike 3.0 Unported License.
//  To view a copy of this license, visit
//  http://creativecommons.org/licenses/by-sa/3.0/
//  or send a letter to Creative Commons, PO Box 1866, Mountain View, CA 94042, USA.


//------------------------------------------------------------------------- SHARED PARAMETERS
$fn=100; // resolution


circleD = 21; // round corner circle diameter
roundR = circleD/2; // round corner circle radius
triangleH = (sqrt(3)*(circleD))/2; // triangle height to calculate other variables

layerHeight = 0.25; // some variariables are multiple of layer height and width
layerWidth = 0.5;

screwExt = 3.4; // screw through hole diameter
verConnectionHoleR = 1.2; // screw thread hole radius
screwHead = 6; // screw head hole diameter

gap = layerHeight/2;

floorHeight = 1.8; // 6*0.25 layer + 0.3 first layer

height = 14; // case height
innerHeight = height - floorHeight*2;

pillarSize = roundR-0.01; // corner pillar size

// dimensions of minkowski's inner square
// these are NOT case dimensions
// to calculate external case dimesions add 2 * roundR
// 55.3 + (2*10.5) = 76.3
width = 55.3 + 30;
wide = 55.3 + 50;

blockLockSize = 2; // middle connection lock size

// side cutting panels size
sidePanelXWidth = wide;
sidePanelYWidth = width;

// screw hole position from centre of the corner round circle
screwHoleRoundR = roundR - layerWidth*4 - (triangleH/2 - layerWidth*4)/2;

// prints dimensions of the case to the console
echo("width", width + roundR*2); // total width
echo("wide", wide + roundR*2); // total wide


// LEONARDO PCB dimensions
pcbWide=53.3;
pcbLenght=68.58;
pcbHeight=1.64;
usbHolePosition=38.1;
usbHeight=7.2 + 2;
usbWide=10.5 + 2;
powerJackPosition=7.62;
powerJackWide=8.9 +2;
powerJackHeight=10.8 +2;

pcbPositionX = width/2 + roundR - layerWidth*7 - gap*4;
pcbPositionZ = 2.5;

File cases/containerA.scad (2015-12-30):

//  ----------------------------------------------------------------------- LICENSE
//  This "3D Printed Case for Arduino Uno, Leonardo" by Zygmunt Wojcik is licensed
//  under the Creative Commons Attribution-ShareAlike 3.0 Unported License.
//  To view a copy of this license, visit
//  http://creativecommons.org/licenses/by-sa/3.0/
//  or send a letter to Creative Commons, PO Box 1866, Mountain View, CA 94042, USA.


include <containerA_params.scad>

//------------------------------------------------------------------------- MODULES
module pcbLeg() {		
	translate([0, 0, 0])
	difference() { 											
		cylinder(h = floorHeight + pcbPositionZ, r1=5.5/2, r2 = 4.5/2);
	}
}


//------------------------------------------------------------------------- MAIN BLOCK
difference()
{
																		// ADD
	union()
	{
		// Add Base
		linear_extrude(height = height/2, convexity = 10)
		minkowski()
		{									
			square([width, wide], center = true);
			circle(roundR);
		}
	}
																		// SUBSTRACT
	union()
	{
		// Lift floor height
		translate([0, 0, floorHeight])
		{
			// Cut Base hole
			linear_extrude(height = height/2, convexity = 10)
			minkowski()
			{
				square([width, wide], center = true);
				circle(roundR - pillarSize);
			}
			// Cut upper block lock
			difference() {
				translate([0, 0, height/2 - floorHeight - blockLockSize]) {
					cylinder(h = blockLockSize+gap, r=width);
				}
				translate([0, 0, height/2 - floorHeight - blockLockSize - gap*2]) {
					linear_extrude(height = blockLockSize+gap*4, convexity = 10)
					minkowski() {
						square([width, wide], center=true);
						circle(roundR - layerWidth*4);
					}
				}
			}
			// Cut x panels 
			for (i = [0 : 180 : 180])				
			rotate([0, 0, i])
			translate([width/2 + roundR - pillarSize/2 - layerWidth*7, 0, 0])
			{
				// Cut X panel hole
				translate([0, 0, height/2])
				cube([pillarSize, sidePanelXWidth, height], center=true);
                
				// Cut X, Y srew holes
				for (i = [wide/2, -wide/2])
				{
					translate([-(roundR - pillarSize/2 - layerWidth*7), i, - floorHeight])
					if (i>0) 
					{
						rotate([0, 0, 45])
						translate([screwHoleRoundR, 0, 0])
						{
							cylinder(h = height*2, r=screwExt/2, center=true);
							cylinder(h = 5,
                                    r1 = (screwHead + (screwHead - screwExt))/2,
                                    r2 = screwExt/2, center=true);
						}
					}
					else
					{
						rotate([0, 0, -45])
						translate([screwHoleRoundR, 0, 0])
						{
							cylinder(h = height*2, r=screwExt/2, center=true);
							cylinder(h = 5,
                                    r1 = (screwHead + (screwHead - screwExt))/2,
                                    r2 = screwExt/2, center=true);
						}
					}
				}
			}
			// Cut Y panels 
			for (i = [90 : 180 : 270])
			rotate([0, 0, i])
			translate([wide/2 + roundR - pillarSize/2 - layerWidth*7, 0, 0])
			{
				// Cut Y panel hole
				translate([0, 0, height/2])
				cube([pillarSize, sidePanelYWidth, height], center=true);
			}
		}
	}
}
//------------------------------------------------------------------------- ADD PCB LEGS
// Translate to pcbPositionX	
translate([-pcbPositionX, -pcbWide/2, 0])

difference()
{
																		// ADD
	union()
	{
		// Add pcb legs
		for(i=[ [10.05, 2.54, 0],
     	    	[10.05, 50.8, 0],
          		[57.04, 35.56, 0],
     	    	[57.04, 7.62, 0] ])
		{
	    		translate(i)
	    		pcbLeg();
		}
	}
																		// SUBSTRACT
	union()
	{
		// Add pcb holders
		for(i=[ [10.05, 2.54, 0],
     	    	[10.05, 50.8, 0],
          		[57.04, 35.56, 0],
     	    	[57.04, 7.62, 0] ])
		{
			translate(i)
			cylinder(h=floorHeight+pcbPositionZ+1.5, r=1.2);
		}
	}
}

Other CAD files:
cases/containerB.scad
cases/containerA_params.scad

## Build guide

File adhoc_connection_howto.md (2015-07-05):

# How-To: WiFi Ad-Hoc connection on RPi

An ad-hoc connection is a peer-to-peer connection, so the configuration should
be the same on all systems.

## No security

Edit `/etc/network/interfaces`:

```
auto wlan0
allow-hotplug wlan0
iface wlan0 inet static
    address STATICIP
    netmask 255.255.255.0
    wireless-channel 1
    wireless-essid MYSSID
    wireless-mode ad-hoc
```

1. You can change your IP address, but I highly suggest using static addresses
   for this kind of connection.  Otherwise you'd have to set up some sort of
   DHCP service like `dhcpcd`.
2. Change SSID.

## WPA

In `/etc/network/interfaces`:

```
auto wlan0
allow-hotplug wlan0
iface wlan0 inet manual
wpa-conf /etc/wpa_supplicant/wpa_supplicant.conf
```

Generate an encrypted passphrase:

```
$ wpa_passphrase MYSSID passphrase
```

Edit `/etc/wpa_supplicant/wpa_supplicant.conf/`:

```
ctrl_interface=DIR=/var/run/wpa_supplicant GROUP=netdev
ap_scan=2
update_config=1

network={
        ssid="MYSSID"
        mode=1
        frequency=2432
        proto=WPA
        key_mgmt=WPA-NONE
        pairwise=NONE
        group=TKIP
        #psk="passphrase"
        psk=encryptedpassphrase
}
```

1. Change your SSID
2. Change your encrypted passphrase to the one that `wpa_passphrase` generated

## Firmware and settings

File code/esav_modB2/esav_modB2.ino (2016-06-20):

// LEDs
const unsigned int red_led_pin = 7;
bool red_led = false;
const unsigned int green_led_pin = 6;
bool green_led = false;

// Remote ON/OFF button
const unsigned int remote_button_pin = 4;

// RELAY (SSR)
const unsigned int relay_pin = 5;

// application states
const unsigned int WAIT = 0;  // wait for first ping (relay is off)
const unsigned int WAIT_FOR_PING = 1;  // wait for ping (relay is on)
const unsigned int PONG = 2;  // answer ping with pong
const unsigned int STOP_REQUEST = 3;  // stop request came
const unsigned int STOP = 4;  // turn the relay off
const unsigned int STOP_RESPONSE = 5; // answer to the stop request
const unsigned int DEBUG = 6;  // turn relay on no matter what

// initial state
unsigned int state = WAIT;

// I/O
const byte EOM = 0x00;
const unsigned int msg_length = 2;
// msg format: 2B msg, 1B EOM

byte in_buffer[msg_length];
byte out_buffer[msg_length];

// counter for number of missed inbound messages
unsigned int no_data_counter = 0;
const unsigned int max_tries = 5;

void setup() {
  // input pins
  pinMode(red_led_pin, OUTPUT);
  pinMode(green_led_pin, OUTPUT);
  pinMode(relay_pin, OUTPUT);
  
  // it may hang so let's pull it up (this inverts logic!)
  pinMode(remote_button_pin, INPUT_PULLUP);

  // start serial connection
  Serial.begin(9600);  // pins 0 and 1
  Serial.setTimeout(1000);

  // initialize pins with desired states
  led(red_led_pin, red_led);
  led(green_led_pin, green_led);
  relay(relay_pin, false);
}

void loop() {
  // reset buffers
  set_buffer(in_buffer, 0x00, 0x00);
  set_buffer(out_buffer, 0x00, 0x00);
  
  // handle debug mode
  if (!debug_on(remote_button_pin) && state == DEBUG) {
    state = WAIT;
  } else if (debug_on(remote_button_pin)) {
    state = DEBUG;
  }

  // wait for the first ping to come (with relay turned off)
  // relay: off
  // red led: on
  // green led: toggle every second
  if (state == WAIT) {
    relay(relay_pin, false);
    red_led = true; led(red_led_pin, red_led);

    if (Serial.available() >= msg_length) {
      // Serial.readBytes(in_buffer, msg_length);
      Serial.readBytesUntil(EOM, in_buffer, msg_length);

      if (is_ping(in_buffer)) {
        state = PONG;
      } else if (is_stop(in_buffer)) {
        state = STOP_REQUEST;
      } else {
        // something's wrong, that's not the correct message
      }

      serial_flush();
    }

    if (state == WAIT) {
      // don't delay if we're decided to go to PONG
      green_led = !green_led; led(green_led_pin, green_led);
      delay(990);
    }
  }

  // wait for cosequtive pings to come (with relay turned on)
  // relay: on
  // red led: off
  // green led: on
  else if (state == WAIT_FOR_PING) {
    relay(relay_pin, true);
    red_led = false; led(red_led_pin, red_led);
    green_led = true; led(green_led_pin, green_led);

    if (Serial.available() >= msg_length) {
      // Serial.readBytes(in_buffer, msg_length);
      Serial.readBytesUntil(EOM, in_buffer, msg_length);

      if (is_ping(in_buffer)) {
        state = PONG;
      } else if (is_stop(in_buffer)) {
        state = STOP_REQUEST;
      } else {
        // something's wrong, that's not the correct message
        delay(990);
      }

      serial_flush();

    } else {
      // no inbound msgs
    }
  }

  // answer PING with PONG
  // relay: keep
  // red led: keep
  // green led: keep
  else if (state == PONG) {
    // fake state, we don't need to do anything
    delay(1000);
    state = WAIT_FOR_PING;
  }

  // someone wants to turn the relay off
  // relay: keep
  // red led: keep
  // green led: off
  else if (state == STOP_REQUEST) {
    green_led = false; led(green_led_pin, green_led);

    state = STOP;
  }

  // turn the relay off
  // relay: off
  // red led: on
  // green led: off
  else if (state == STOP) {
    relay(relay_pin, false);
    red_led = true; led(red_led_pin, red_led);
    green_led = false; led(green_led_pin, green_led);
    
    state = STOP_RESPONSE;
    delay(100);
  }

  // answer to the stop request
  // relay: keep
  // red led: keep
  // green led: keep
  else if (state == STOP_RESPONSE) {
    // fake state, we don't need to do anything
    delay(100);
    state = STOP;
  }

  // enable the relay
  // relay: on
  // red led: quickly toggle
  // green led: quickly toggle with other phase than red led
  else if (state == DEBUG) {
    relay(relay_pin, true);
    red_led = !red_led; led(red_led_pin, red_led);
    green_led = !red_led; led(green_led_pin, green_led);

    state = DEBUG;
    serial_flush_all();
    delay(500);
  }

  else {
    // unknown state, let's stop
    state = STOP;
  }

}

void relay(const unsigned int pin, const bool state) {
  if (state)
    digitalWrite(pin, HIGH);
  else
    digitalWrite(pin, LOW);
}

void led(const unsigned int pin, const bool state) {
  if (state)
    digitalWrite(pin, HIGH);
  else
    digitalWrite(pin, LOW);
}

bool debug_on(const unsigned int pin) {
  // Decide if debug mode should be on based on pin state.
  return digitalRead(pin);
}

bool is_ping(byte *buf) {
  return buf[0] == 0xAA && buf[1] == 0x00;
}

bool is_stop(byte *buf) {
  return buf[0] == 0xFF && buf[1] == 0x00;
}

void serial_flush() {
  // Since Arduino 1.0, the Serial.flush() only removes outgoing data,
  // not incoming. This function only drops messages from incoming buffer
  // and only up to termination char.
  int ch;
  while (Serial.available() > 0) {
    ch = Serial.read();

    // flush only incomplete package
    if (ch == EOM) {
      break;
    }
  }
}

void serial_flush_all() {
  // Since Arduino 1.0, the Serial.flush() only removes outgoing data,
  // not incoming. This function all leftover chars in the incoming buffer.
  int ch;
  while (Serial.available() > 0) {
    ch = Serial.read();
  }
}

void set_buffer(byte *buf, byte b0, byte b1) {
  buf[0] = b0;
  buf[1] = b1;
}

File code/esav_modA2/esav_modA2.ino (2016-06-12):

// LEDs
const unsigned int green_led_pin = 7;
bool green_led = false;

// STOP button pin
const unsigned int stop_pin = 2;

// application states
const unsigned int INITIAL_PING = 0;
const unsigned int PING = 1;
const unsigned int PONG = 2;
const unsigned int STOP_REQUEST = 3;
const unsigned int STOP_RESPONSE = 4;

// initial state
unsigned int state = INITIAL_PING;

// counters
unsigned int stop_counter = 0;  // count how many times stop was sent

// I/O
const byte EOM = 0x00;
const unsigned int msg_length = 2;
// msg format: 2B msg, 1B eom

byte in_buffer[msg_length];
byte out_buffer[msg_length];

// for handling emergency interrupt
volatile bool emergency = false;

void setup() {
  // input pins
  pinMode(green_led_pin, OUTPUT);
  pinMode(stop_pin, INPUT);
  
  // start serial connection
  Serial.begin(9600);  // pins 0 and 1
  Serial.setTimeout(1000);

  // initialize pins with desired states
  led(green_led_pin, green_led);

  // set interrupt function on STOP pin
  attachInterrupt(digitalPinToInterrupt(stop_pin), emergencyInterrupt, RISING);
}

void loop() {
  // reset buffers
  set_buffer(in_buffer, 0x00, 0x00);
  set_buffer(out_buffer, 0x00, 0x00);

  if (emergency) {
    state = STOP_REQUEST;
    emergency = false;
  }

  // send ping every second
  // green led: toggle every second
  if (state == INITIAL_PING) {
    set_buffer(out_buffer, 0xAA, EOM);
    Serial.write(out_buffer, msg_length);

    if (Serial.available() >= msg_length) {
      // Serial.readBytes(in_buffer, msg_length);
      Serial.readBytesUntil(EOM, in_buffer, msg_length);

      if (is_pong(in_buffer)) {
        state = PONG;
      } else {
        // wrong pong format
      }
      serial_flush();
    }
    
    green_led = !green_led; led(green_led_pin, green_led);
    delay(1000);
  }

  // send ping every second
  // green led: on at all times
  else if (state == PING) {
    green_led = true; led(green_led_pin, green_led);
    
    set_buffer(out_buffer, 0xAA, EOM);
    Serial.write(out_buffer, msg_length);

    delay(1000);

    if (Serial.available() >= msg_length) {
      // Serial.readBytes(in_buffer, msg_length);
      Serial.readBytesUntil(EOM, in_buffer, msg_length);

      if (is_pong(in_buffer)) {
        state = PONG;
      } else {
        // wrong pong format
      }
      serial_flush();
    }
  }

  // PONG msg came back!
  // green led: keep
  else if (state == PONG) {
    state = PING;
  }

  // STOP button pushed
  // green led: pulse 10x quickly
  else if (state == STOP_REQUEST) {
    if (stop_counter++ >= 10) {
      stop_counter = 0;
      state = INITIAL_PING;
    } else {
      green_led = !green_led; led(green_led_pin, green_led);
      set_buffer(out_buffer, 0xFF, EOM);
      Serial.write(out_buffer, msg_length);

      state = STOP_RESPONSE;
      delay(50);
    }
  }

  // module B responded for STOP
  // green led: keep
  else if (state == STOP_RESPONSE) {
    // this is fake
    state = STOP_REQUEST;
  }

  else {
    // unknown state, switch to INIT_PING?
    state = INITIAL_PING;
  }
}

void emergencyInterrupt() {
  emergency = true;
}

void led(const unsigned int pin, const bool state) {
  if (state)
    digitalWrite(pin, HIGH);
  else
    digitalWrite(pin, LOW);
}

bool is_pong(byte *buf) {
  return buf[0] == 0xCC && buf[1] == 0x00;
}

void serial_flush() {
  // Since Arduino 1.0, the Serial.flush() only removes outgoing data,
  // not incoming. This function only drops messages from incoming buffer
  // and only up to termination char.
  int ch;
  while (Serial.available() > 0) {
    ch = Serial.read();

    // flush only incomplete package
    if (ch == EOM) {
      break;
    }
  }
}

void set_buffer(byte *buf, byte b0, byte b1) {
  buf[0] = b0;
  buf[1] = b1;
}

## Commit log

2015-07-05 Sources for simple socket ping
2015-09-16 Reset scaffolding for modA
    [moduleA.py]
2015-09-16 Lighting LED when sending PING
2015-09-19 Switch to constant-regulated pin numbers
2015-09-19 Working stop-reset && ping-pong
    [moduleA.py, moduleB.py]
2015-09-19 Added Fritzing schemas of both modules
    [schema_moduleA.fzz, schema_moduleB.fzz]
2015-09-28 Updated wire colors
    [schema_moduleA.fzz, schema_moduleB.fzz]
2015-10-27 Added module A schematics + work on project description
2015-10-27 Switch schema A to arduino
    [schema_moduleA.fzz]
2015-11-02 Better schema for modA with radio comm.
    [schema_moduleA.fzz]
2015-11-02 Sample files for Arduino communication
2015-11-04 Updated schemas (breadboard images)
    Additionally module A has better schematics schema.
    [schema_moduleA.fzz, schema_moduleB.fzz]
2015-11-04 Stateflow in Arduino: basic working
2015-11-12 Get state machines to work, support emergency interruption
2015-11-14 Added photos, biblio, indices of photos and schemas
    New photos: car, arduino, contactor
    Bibliography: only one entry for now
2015-11-17 Adapt modB.ino to Arduino Pro + add logic for missing packages data
2015-11-18 Renaming and moving stuff around
    [schema_moduleA.fzz, schema_moduleB.fzz]
2015-11-18 Updated "Power" subchapter
2015-11-18 Updated schemas for module A and B
    [schema_moduleA.fzz, schema_moduleB.fzz]
2015-11-18 Switched bigger pictures with scaled down versions
2015-11-18 modB: Fix counting when data is not coming
    Error was: only 2 seconds passed before module B turned off.
    Now the counting happens in different place so we count correctly to 3.
    [esav_modB.ino]
2015-11-18 Vertical schemas, requirement traceability matrix
2015-11-22 Traceability matrix: add missing (sub)chapters
2015-11-28 Add details about new relay ASR-90DD-H
2015-12-02 Encryption, chassis, programming Arduino
2015-12-05 1 more paragraph in turning on/off the engine
    + missing pic of the relay
2015-12-05 Added section about cable for programming Arduino Pro
2015-12-05 Updated requirements traceability matrix
2015-12-07 Add indents on para.'s first lines, italics for agreement
2015-12-21 Add thermovision camera data
    [flir_pomiary.ods]
2015-12-29 Remove OLD files, add updates schemas and thesis
    The thesis is going to be removed anyway.
    [schema_moduleA.fzz, schema_moduleB.fzz]
2015-12-30 Added more to the section about programming cable
2015-12-30 Add biblio for Romoss powerbank
2015-12-30 Fix some comments in the traceability matrix
2015-12-30 Add module cases
    [containerA.scad, containerA.stl, containerA_params.scad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]
2016-01-07 Part 2 of fixes suggested by supervisor
    This one changes requirements lists:
    * they have section numbering
    * they have labels
    * they're cross referenced from req. traceability matrix
2016-01-07 Fix figure for USB-UART converter
2016-01-07 Fix req. traceability matrix 'chapter' header
2016-01-07 Switching numbers to siunitx package
2016-01-08 Chapter1: switch '—' to double dash '--'
2016-02-17 Switch to ReadBytes in both modules
    ReadBytes is safer since we're using the stop character in the
    message contents.
    The stop character is 0x00, and we can have messages like
    0x22000100.
2016-02-17 Code cleanup & counter reset
    Counter is reset in every state except for RUN/PING.
    Code cleanup: removed unnecessary whitespace indents.
    Removed one function that was never used from module B code.
    [esav_modA.ino, esav_modB.ino]
2016-02-17 Module B: drop delay in WAIT if switching to RUN
    Drop `delay(1100)` call if we're switching to RUN. This removes the
    unnecessary wait time during which module A probably dissynchronises
    counter with module B.
    Additional change: bigger delay (1000→1100). This makes sure we get more
    messages from module A (it may be a not important change since flushing
    was introduced in parent commit, but I like it anyway).
2016-03-30 Add REMOTE button for module B
    REMOTE button turns on/off the need for remote module A.
    Ie. with REMOTE turned off, we can run the vehicle...
2016-06-20 Fix locking in STOP after STOP→DEBUG→WAIT
    [esav_modB2.ino]
